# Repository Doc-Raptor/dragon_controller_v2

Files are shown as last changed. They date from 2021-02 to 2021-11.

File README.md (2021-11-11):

This is a controller-board for 3d printers based on the LPC1768 and has five tmc2209 onboard. It is made for the Marlin Firmware and RepRapFirmware. It has a Port to plug a Demos D1 Mini directly on it or a Raspberry Pi can be connected to with just jumpercables (no resistors needed).
IT IS NOT FULLY TESTED!!!
NO FURTHER DEVELOPMENT. RepRapFirmware discountinues support for the LPC1768

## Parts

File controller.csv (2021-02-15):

ID | Bezeichner | Gehäuse | Stückzahl | Bezeichnung | Anbieter und Referenz
1 | J1 | PinHeader_1x07_P2.54mm_Vertical | 1 | EXP3
2 | R9,R26,R25,R23,R20,R16,R15,R13,R10,R8 | R_1206_3216Metric | 10 | 0R11
3 | R37,R22,R21,R18,R12,R36 | R_1206_3216Metric | 6 | 4K7
4 | J24 | PinHeader_1x03_P2.54mm_Vertical | 1 | TH_E1
5 | C59,C16,C15,C19 | C_1206_3216Metric | 4 | 10uF
6 | Y1 | Crystal_SMD_5032-2Pin_5.0x3.2mm | 1 | 12Mhz
7 | U8,U7,U6,U5,U4 | QFN-28-1EP_5x5mm_P0.5mm_EP3.35x3.35mm_ThermalVias | 5 | TMC2209-LA
8 | U2 | LQFP-100_14x14mm_P0.5mm | 1 | LPC1768FBD100
9 | U1 | SOT-23-6 | 1 | MP2451
10 | SW1 | SW_Push_SPST_NO_Alps_SKRK | 1 | SW_Push
11 | R34,R33 | R_1206_3216Metric | 2 | 33K
12 | R32 | R_1206_3216Metric | 1 | 1K5
13 | R31,R30,R29,R28,R7,R3 | R_1206_3216Metric | 6 | 10K
14 | R27,R24,R19,R14,R6,R2 | R_1206_3216Metric | 6 | 1K
15 | R17,R11,R35 | R_1206_3216Metric | 3 | 100
16 | Q5 | SOT-23 | 1 | IRLML2244
17 | Q3,Q1,Q4 | TO-263-3_TabPin2 | 3 | SE30150
18 | Q2 | SOT-23 | 1 | PMV40UN2
19 | L2 | L_0805_2012Metric | 1 | 22uH
20 | J20 | PinHeader_1x04_P2.54mm_Vertical | 1 | e0-Stepper
21 | J44 | PinHeader_1x04_P2.54mm_Vertical | 1 | z-Stepper
22 | J43 | PinHeader_1x02_P2.54mm_Vertical | 1 | VCC
23 | J39 | PinHeader_1x04_P2.54mm_Vertical | 1 | y-Stepper
24 | J33 | PinHeader_1x04_P2.54mm_Vertical | 1 | x-Stepper
25 | J32 | microSD_HC_Hirose_DM3AT-SF-PEJM5 | 1 | Micro_SD_Card
26 | J31 | PinHeader_1x04_P2.54mm_Vertical | 1 | Serial
27 | J30 | PinHeader_2x05_P2.54mm_Vertical | 1 | EXP2
28 | J29 | PinHeader_2x05_P2.54mm_Vertical | 1 | EXP1
29 | J22 | PinHeader_1x02_P2.54mm_Vertical | 1 | USB_5V
30 | J21 | PinHeader_1x04_P2.54mm_Vertical | 1 | USB
31 | J19 | PinHeader_1x04_P2.54mm_Vertical | 1 | e1-Stepper
32 | J18 | PinHeader_1x01_P2.54mm_Vertical | 1 | DIAG_E1
33 | J17 | PinHeader_1x03_P2.54mm_Vertical | 1 | X-
34 | J16 | PinHeader_1x03_P2.54mm_Vertical | 1 | MAX_END
35 | J15 | PinHeader_1x03_P2.54mm_Vertical | 1 | Y-
36 | J13 | PinHeader_1x03_P2.54mm_Vertical | 1 | Z-
37 | J12 | PinHeader_1x02_P2.54mm_Vertical | 1 | DIAG_Z
38 | J11 | PinHeader_1x02_P2.54mm_Vertical | 1 | DIAG_Y
39 | J10 | PhoenixContact_GMSTBVA_2,5_2-G-7,62_1x02_P7.62mm_Vertical | 1 | Power_Heat
40 | J9 | PinHeader_1x01_P2.54mm_Vertical | 1 | DIAG_E0
41 | J8 | PinHeader_1x02_P2.54mm_Vertical | 1 | Fan_Cooler
42 | J7 | PinHeader_1x03_P2.54mm_Vertical | 1 | SV1
43 | J6 | PinHeader_1x03_P2.54mm_Vertical | 1 | TH_B
44 | J5,J23 | PhoenixContact_MCV_1,5_2-G-5.08_1x02_P5.08mm_Vertical | 2 | Hotend
45 | J4 | PinHeader_1x02_P2.54mm_Vertical | 1 | DIAG_X
46 | J3 | PhoenixContact_GMSTBVA_2,5_2-G-7,62_1x02_P7.62mm_Vertical | 1 | Power_IN
47 | J2 | PinHeader_1x03_P2.54mm_Vertical | 1 | TH_E0
48 | H4,H3,H2,H1 | MountingHole_3.2mm_M3 | 4 | MountingHole
49 | F1 | Fuseholder_Blade_ATO_Littelfuse_Pudenz_2_Pin | 1 | Fuse_Power
50 | D11,D8,D2,D3 | D_SOD-123 | 4 | 1N5819
51 | C58,C57,C17,C14 | C_0603_1608Metric | 4 | 12pF
52 | C56,C45,C39,C33,C27 | C_1206_3216Metric | 5 | 2.2uF
53 | C55,C54,C52,C51,C49,C48,C47,C46,C43,C42,C41,C40,C37,C36,C35,C34,C31,C30,C29,C25,C18,C1 | C_1206_3216Metric | 22 | 100nF
54 | C53,C26,C24,C22,C20 | CP_Elec_6.3x7.7 | 5 | 100uF
55 | C50,C44,C38,C32,C28 | C_0603_1608Metric | 5 | 22nF
56 | C23,C21,C13,C12,C11,C10,C9,C8,C7,C6 | C_0805_2012Metric | 10 | 0.1uF
57 | J46 | PinHeader_1x02_P2.54mm_Vertical | 1 | 3.3V
58 | J45 | PinHeader_1x02_P2.54mm_Vertical | 1 | 5V
59 | C2 | C_1206_3216Metric | 1 | 4.7uF
60 | C3,C4 | C_0805_2012Metric | 2 | 1uF
61 | C5 | C_0603_1608Metric | 1 | 33pF
62 | D1 | D_SMA | 1 | B140-13-F
63 | L1 | L_1812_4532Metric | 1 | 4.7uH
64 | R1 | R_1206_3216Metric | 1 | 124K
65 | R4 | R_1206_3216Metric | 1 | 23K7
66 | U3 | SOT-23-5 | 1 | RT9013-33GB
67 | R5 | R_1206_3216Metric | 1 | 100K
68 | TP1 | TestPoint_Pad_D1.0mm | 1 | RT1
69 | TP2 | TestPoint_Pad_D1.0mm | 1 | RT2
70 | TP3 | TestPoint_Pad_D1.0mm | 1 | RO
71 | TP4 | TestPoint_Pad_D1.0mm | 1 | TCK
72 | TP5 | TestPoint_Pad_D1.0mm | 1 | TRS
73 | TP6 | TestPoint_Pad_D1.0mm | 1 | TMS
74 | TP7 | TestPoint_Pad_D1.0mm | 1 | TDI
75 | TP8 | TestPoint_Pad_D1.0mm | 1 | TDO
76 | TP9 | TestPoint_Pad_D1.0mm | 1 | RTK

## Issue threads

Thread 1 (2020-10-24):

Und läuft es...

leseaw, 2020-10-24:
Moin Meister,
es sieht ja ganz guta us von der Idee her.
Nur funktioniert es auch?
Oder eher noch pre-apha??

Doc-Raptor, 2021-01-23:
Ich habe gestern geschaft, das der Mikrocontroller den Bootloader angenommen hat. Ich habe für eine Zeit das Projekt pausiert, damit ich nach einiger Zeit mit einem klaren Kopf drangehen zu können. Ich habe es aber auch dann nicht geschaft, das der Mikrocontroller funktionierte, also habe ich in mehreren Foren gefragt. Meistens kamen die nur mit irgendwelchen Tutorial, wie man mit Flash Magic das Ding flasht, die ich schon kannte, bis einer im eevblog Forum empfohlen hat, den Bootpin auf Low für den Flashvorgang auf Low zu halten anstatt wie überall steht den nur nach dem man Reset gedrückt hat kurzdarauf den Bootpin wieder loszulassen und dann den Flashvorgang zu starten. Ich bin auch dabei das Board paar Änderungen zu verpassen, was ein neues Board bedeutet. Der Teil mit den Stepper Drivern ist noch nicht getestet, ich hofe aber das ich das nächste Woche schaffe, wenn die Chips da sind.

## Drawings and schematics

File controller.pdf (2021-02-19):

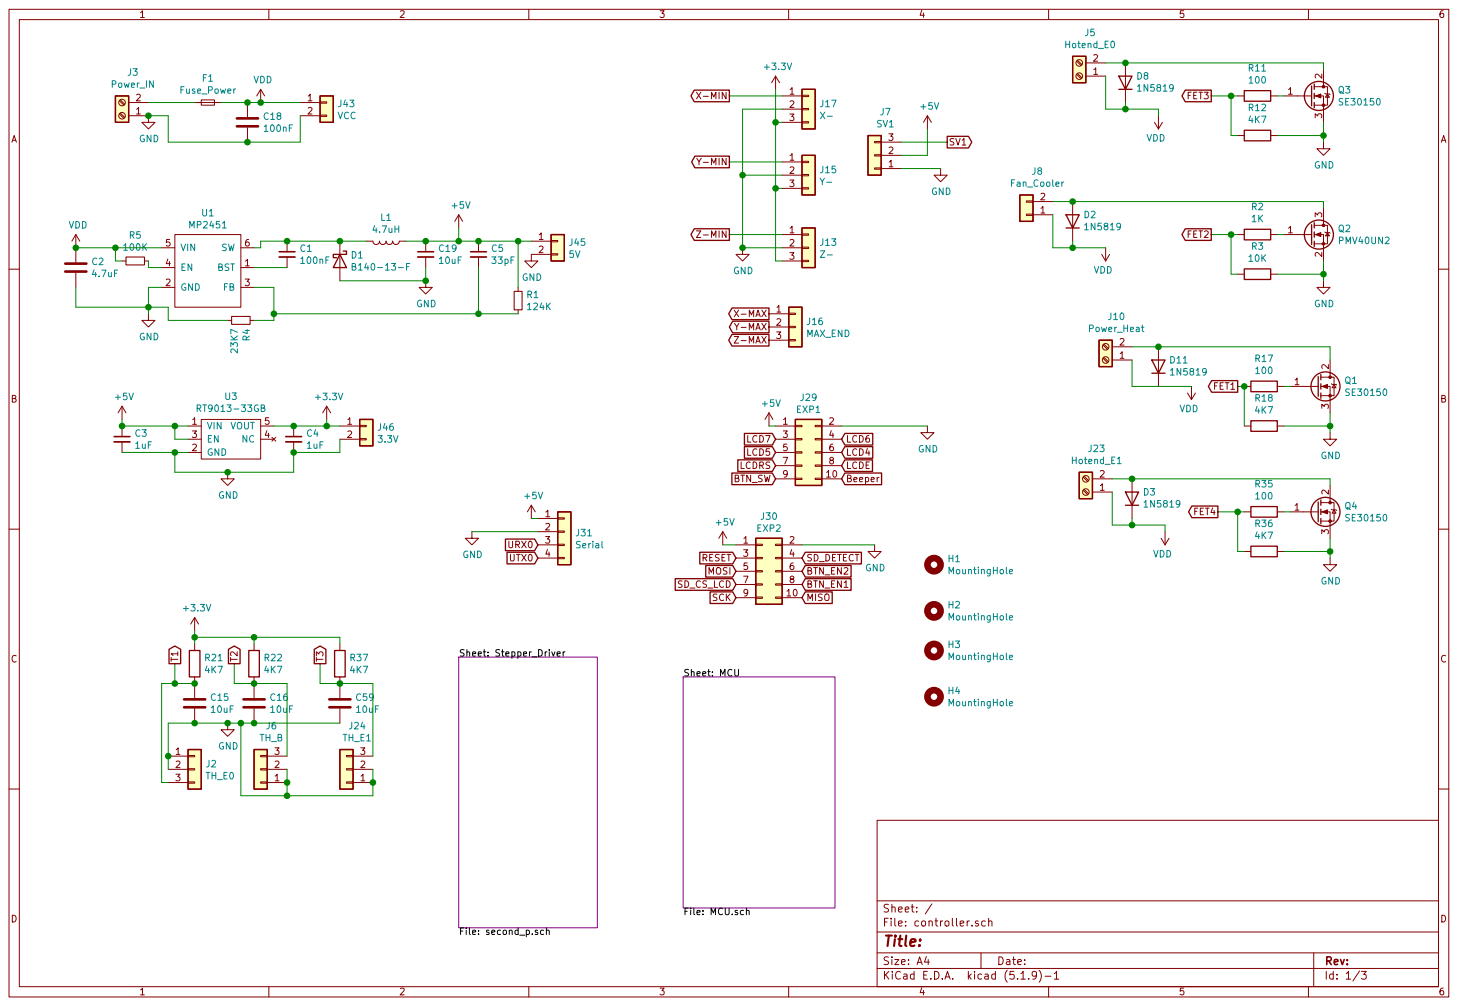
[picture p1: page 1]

File: MCU.sch Sheet: Stepper_Driver

Id: 1/3 Title: File: controller.sch Sheet: / Sheet: MCU

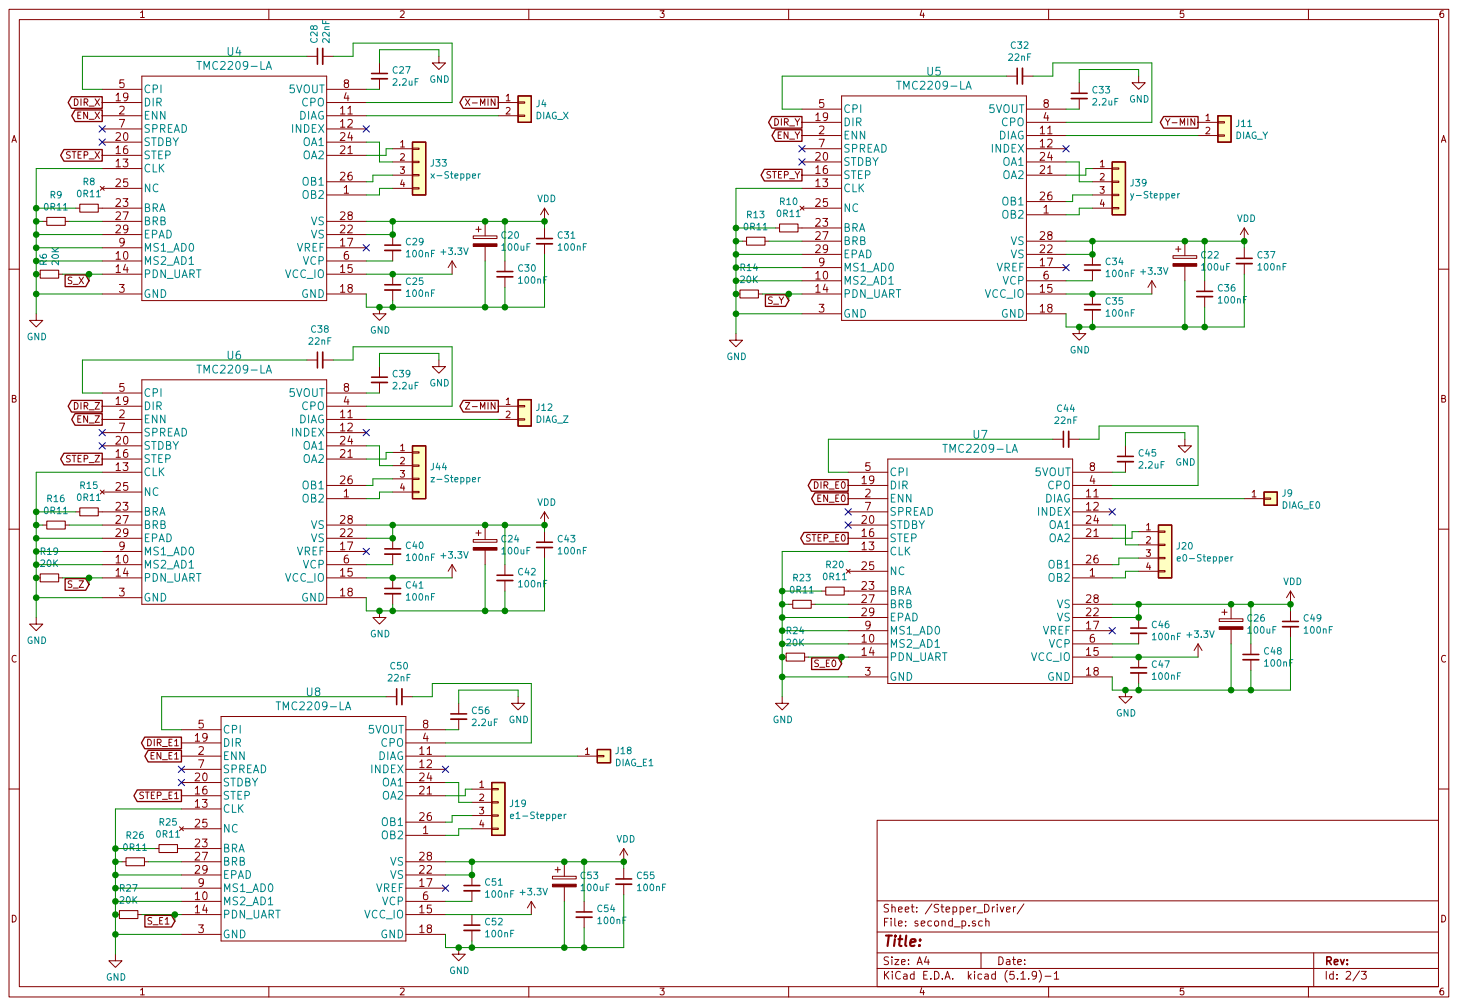
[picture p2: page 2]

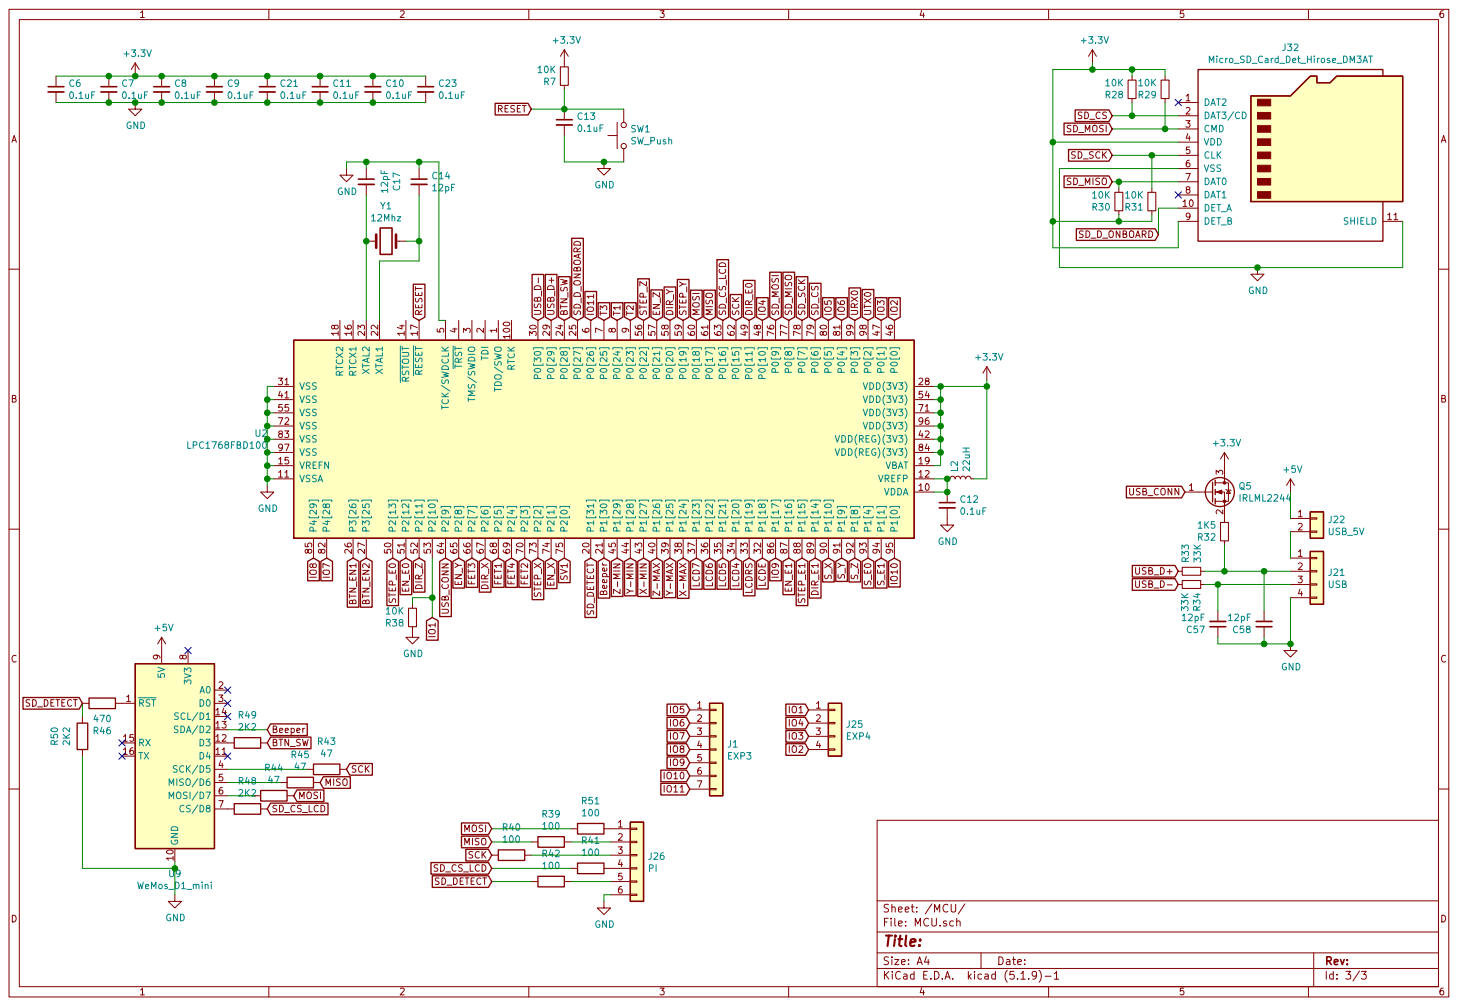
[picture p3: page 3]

1 VDDA 10 RTCK 100 VSSA 11 VREFP 12 RSTOUT 14 VREFN 15 RTCX1 16 RESET 17 RTCX2 18 VBAT 19 TDI 2 P1[31] 20 P1[30] 21 XTAL1 22 XTAL2 23 P0[28] 24 P0[27] 25 P3[26] 26 P3[25] 27

4 P1[26] 40 VSS 41 VDD(REG)(3V3) 42 P1[27] 43 P1[28] 44 P1[29] 45 P0[0] 46 P0[1] 47 P0[10] 48 P0[11] 49 TCK/SWDCLK

Id: 3/3 Title: File: MCU.sch Sheet: /MCU/

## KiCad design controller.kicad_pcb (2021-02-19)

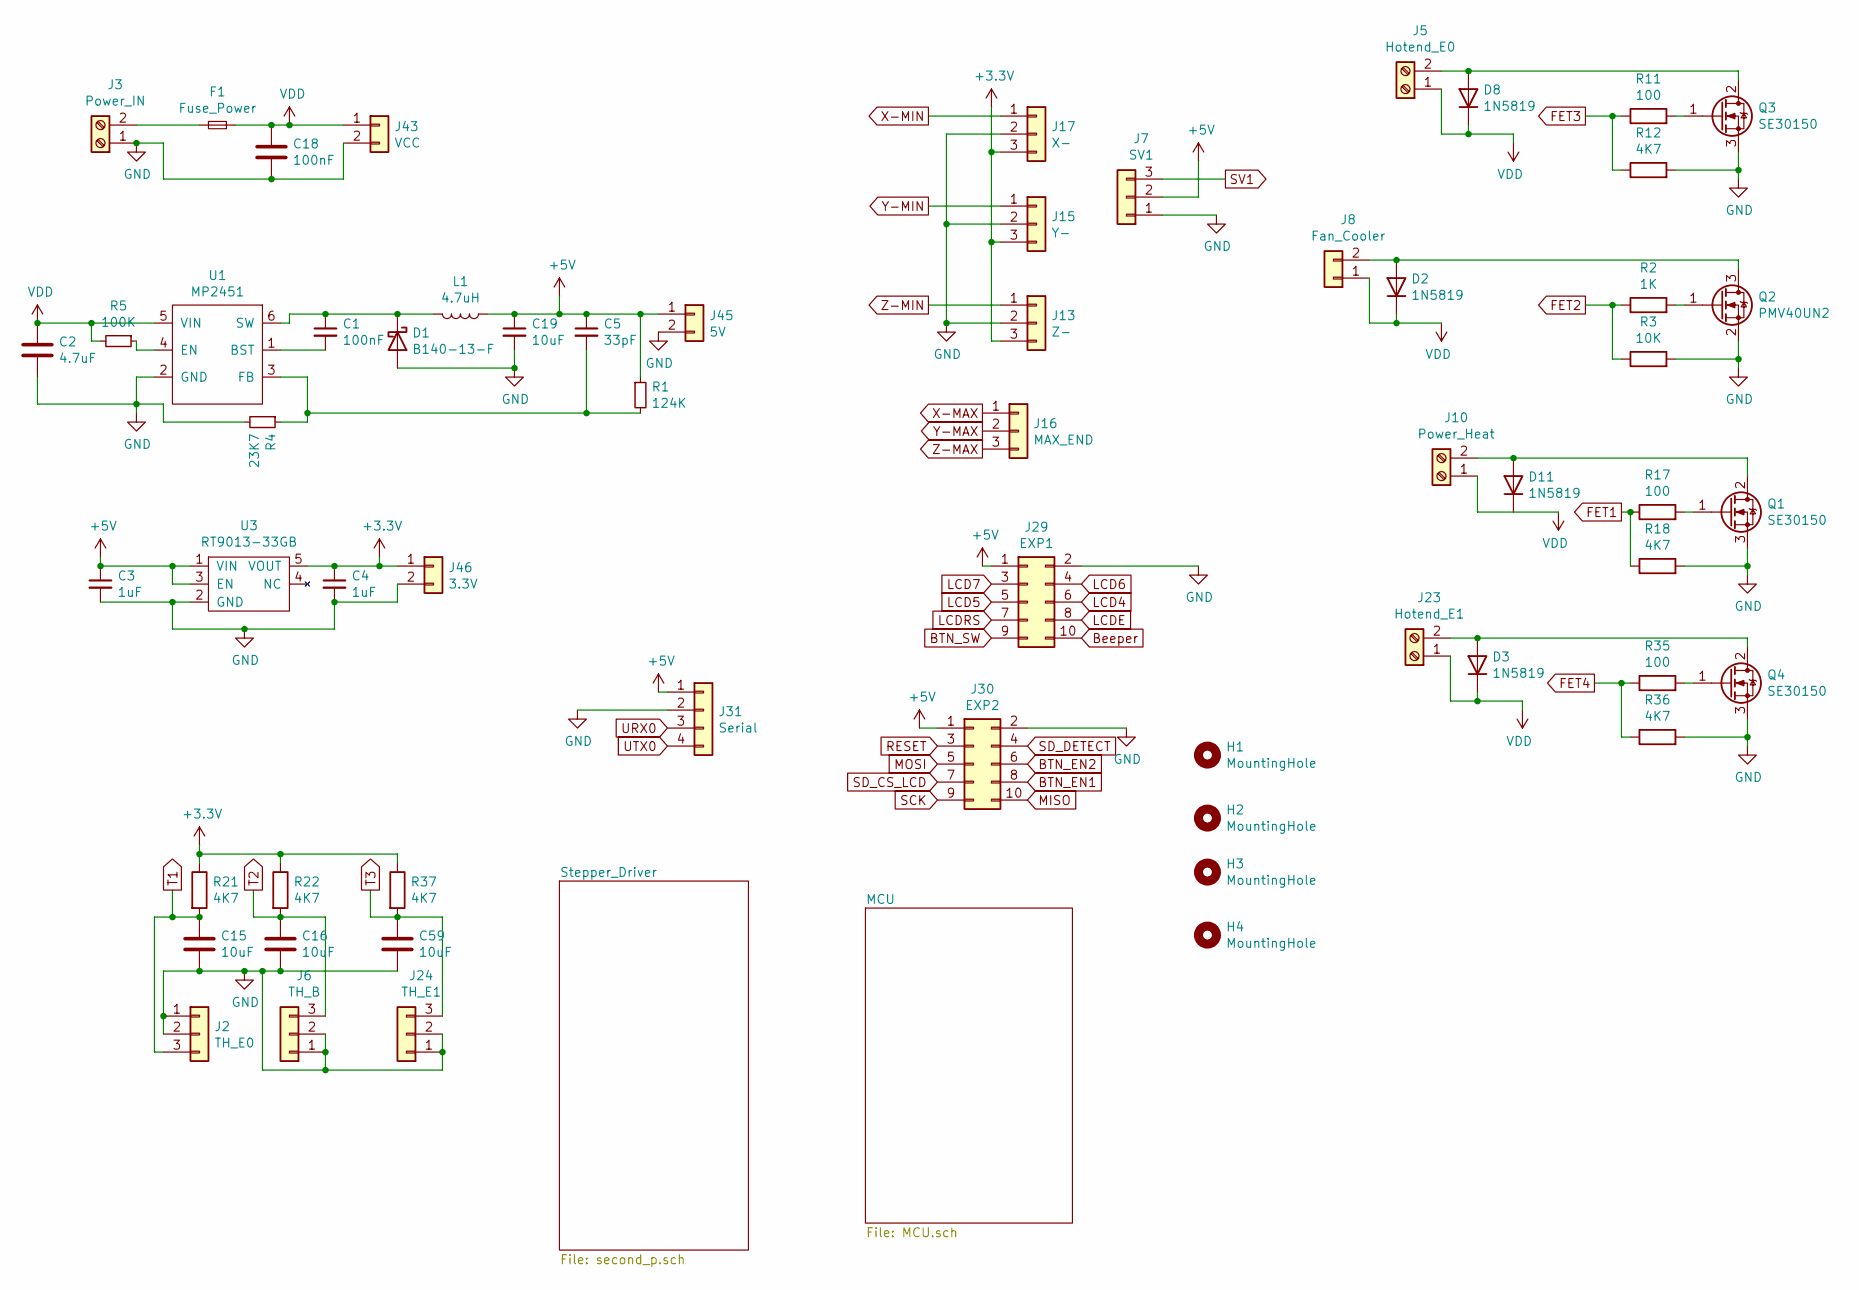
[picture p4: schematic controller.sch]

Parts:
C1, C18: 100nF; C_1206_3216Metric
C2: 4.7uF; C_1206_3216Metric
C3, C4: 1uF; C_0805_2012Metric
C5: 33pF; C_0603_1608Metric
C15, C16, C19, C59: 10uF; C_1206_3216Metric
D1: B140-13-F; D_SMA
D2, D3, D8, D11: 1N5819; D_SOD-123
F1: Fuse_Power; Fuseholder_Blade_Mini_Keystone_3568
H1, H2, H3, H4: MountingHole; MountingHole_3.2mm_M3
J2: TH_E0; PinHeader_1x03_P2.54mm_Vertical
J3: Power_IN; PhoenixContact_GMSTBVA_2,5_2-G-7,62_1x02_P7.62mm_Vertical
J5: Hotend_E0; PhoenixContact_MCV_1,5_2-G-5.08_1x02_P5.08mm_Vertical
J6: TH_B; PinHeader_1x03_P2.54mm_Vertical
J7: SV1; PinHeader_1x03_P2.54mm_Vertical
J8: Fan_Cooler; PinHeader_1x02_P2.54mm_Vertical
J10: Power_Heat; PhoenixContact_GMSTBVA_2,5_2-G-7,62_1x02_P7.62mm_Vertical
J13: Z-; PinHeader_1x03_P2.54mm_Vertical
J15: Y-; PinHeader_1x03_P2.54mm_Vertical
J16: MAX_END; PinHeader_1x03_P2.54mm_Vertical
J17: X-; PinHeader_1x03_P2.54mm_Vertical
J23: Hotend_E1; PhoenixContact_MCV_1,5_2-G-5.08_1x02_P5.08mm_Vertical
J24: TH_E1; PinHeader_1x03_P2.54mm_Vertical
J29: EXP1; Multicomp_MC9A12-1034_2x05_P2.54mm_Vertical
J30: EXP2; Multicomp_MC9A12-1034_2x05_P2.54mm_Vertical
J31: Serial; PinHeader_1x04_P2.54mm_Vertical
J43: VCC; PinHeader_1x02_P2.54mm_Vertical
J45: 5V; PinHeader_1x02_P2.54mm_Vertical
J46: 3.3V; PinHeader_1x02_P2.54mm_Vertical
L1: 4.7uH; L_1812_4532Metric
Q1, Q3, Q4: SE30150; TO-263-3_TabPin2
Q2: PMV40UN2; SOT-23
R1: 124K; R_1206_3216Metric
R2: 1K; R_1206_3216Metric
R3: 10K; R_1206_3216Metric
R4: 23K7; R_1206_3216Metric
R5: 100K; R_1206_3216Metric
R11, R17, R35: 100; R_1206_3216Metric
R12, R18, R21, R22, R36, R37: 4K7; R_1206_3216Metric
U1: MP2451; SOT-23-6
U3: RT9013-33GB; SOT-23-5

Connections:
+3V3: C4.1, J13.3, J15.3, J17.3, J46.1, R21.1, R22.1, R37.1, U3.5 (VOUT); also elsewhere on the board
+5V: C3.1, C5.1, C19.1, J7.2, J29.1, J30.1, J31.1, J45.1, L1.1, R1.1, U3.1 (VIN), U3.3 (EN); also elsewhere on the board
BTN_EN1: J30.8; also elsewhere on the board
BTN_EN2: J30.6; also elsewhere on the board
BTN_SW: J29.9; also elsewhere on the board
Beeper: J29.10; also elsewhere on the board
FET1: R17.1, R18.1; also elsewhere on the board
FET2: R2.1, R3.1; also elsewhere on the board
FET3: R11.1, R12.1; also elsewhere on the board
FET4: R35.1, R36.1; also elsewhere on the board
GND: C2.2, C3.2, C4.2, C15.2, C16.2, C18.2, C19.2, C59.2, D1.2 (A), J2.1, J2.2, J3.1, J6.1, J6.2, J7.1, J13.2, J15.2, J17.2, J24.1, J24.2, J29.2, J30.2, J31.2, J43.2, J45.2, J46.2, Q1.3 (S), Q2.2 (S), Q3.3 (S), Q4.3 (S), R3.2, R4.2, R12.2, R18.2, R36.2, U1.2 (GND), U3.2 (GND); also elsewhere on the board
LCD4: J29.6; also elsewhere on the board
LCD5: J29.5; also elsewhere on the board
LCD6: J29.4; also elsewhere on the board
LCD7: J29.3; also elsewhere on the board
LCDE: J29.8; also elsewhere on the board
LCDRS: J29.7; also elsewhere on the board
MISO: J30.10; also elsewhere on the board
MOSI: J30.5; also elsewhere on the board
unnamed: C1.1, D1.1 (K), L1.2, U1.6 (SW)
unnamed: C1.2, U1.1 (BST)
unnamed: C5.2, R1.2, R4.1, U1.3 (FB)
unnamed: D2.2 (A), J8.2, Q2.3 (D)
unnamed: D3.2 (A), J23.2, Q4.2 (D)
unnamed: D8.2 (A), J5.2, Q3.2 (D)
unnamed: D11.2 (A), J10.2, Q1.2 (D)
unnamed: F1.1, J3.2
unnamed: Q1.1 (G), R17.2
unnamed: Q2.1 (G), R2.2
unnamed: Q3.1 (G), R11.2
unnamed: Q4.1 (G), R35.2
unnamed: R5.1, U1.4 (EN)
RESET: J30.3; also elsewhere on the board
SCK: J30.9; also elsewhere on the board
SD_CS_LCD: J30.7; also elsewhere on the board
SD_DETECT: J30.4; also elsewhere on the board
SV1: J7.3; also elsewhere on the board
T1: C15.1, J2.3, R21.2; also elsewhere on the board
T2: C16.1, J6.3, R22.2; also elsewhere on the board
T3: C59.1, J24.3, R37.2; also elsewhere on the board
URX0: J31.3; also elsewhere on the board
UTX0: J31.4; also elsewhere on the board
VDD: C2.1, C18.1, D2.1 (K), D3.1 (K), D8.1 (K), D11.1 (K), F1.2, J5.1, J8.1, J10.1, J23.1, J43.1, R5.2, U1.5 (VIN); also elsewhere on the board
X-MAX: J16.1; also elsewhere on the board
X-MIN: J17.1; also elsewhere on the board
Y-MAX: J16.2; also elsewhere on the board
Y-MIN: J15.1; also elsewhere on the board
Z-MAX: J16.3; also elsewhere on the board
Z-MIN: J13.1; also elsewhere on the board

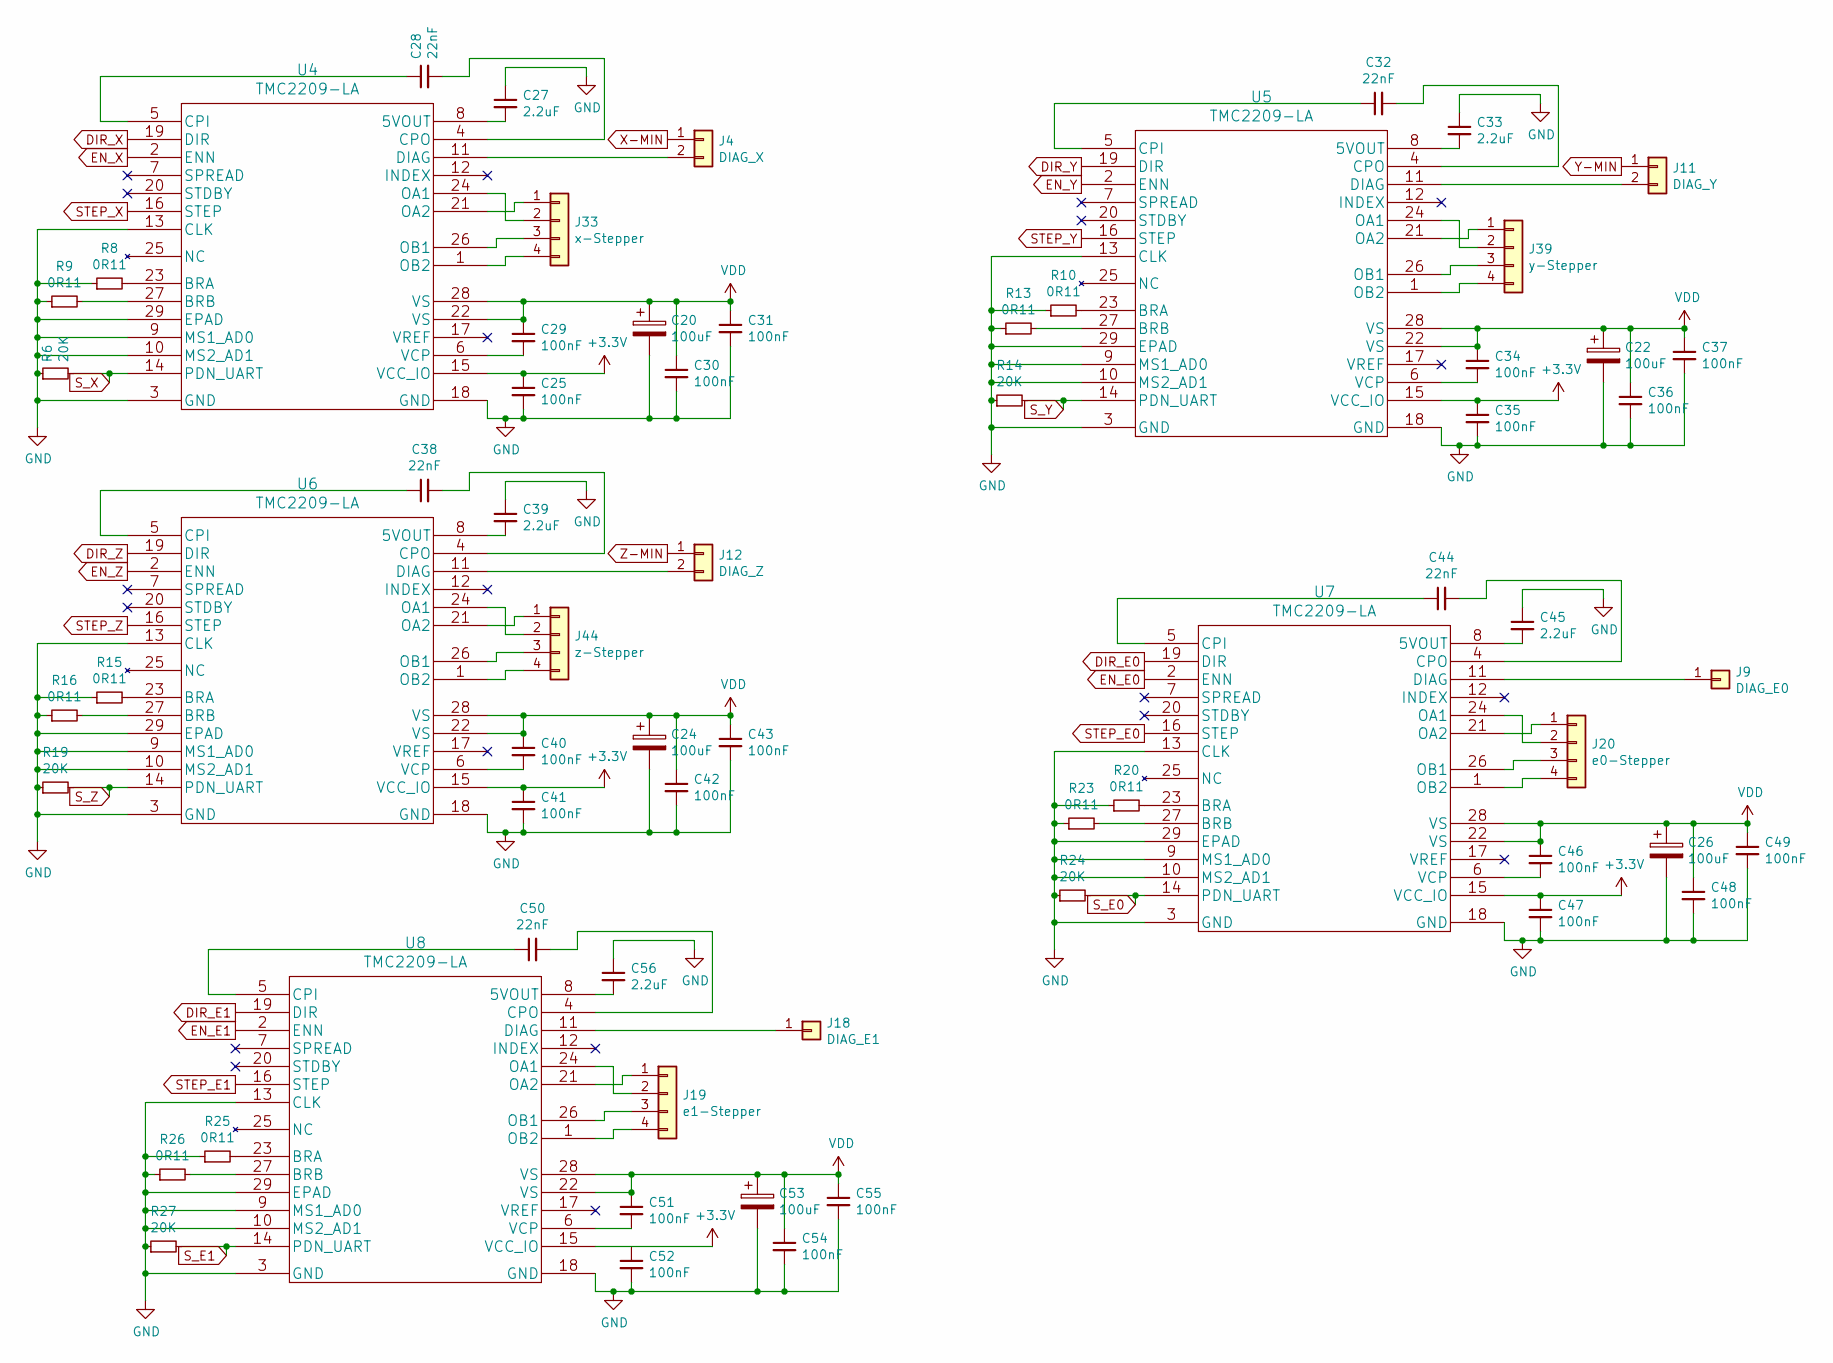
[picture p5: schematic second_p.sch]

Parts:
C20, C22, C24, C26, C53: 100uF; CP_Elec_6.3x7.7
C25, C29, C30, C31, C34, C35, C36, C37, C40, C41, C42, C43, C46, C47, C48, C49, C51, C52, C54, C55: 100nF; C_1206_3216Metric
C27, C33, C39, C45, C56: 2.2uF; C_1206_3216Metric
C28, C32, C38, C44, C50: 22nF; C_0603_1608Metric
J4: DIAG_X; PinHeader_1x02_P2.54mm_Vertical
J9: DIAG_E0; PinHeader_1x01_P2.54mm_Vertical
J11: DIAG_Y; PinHeader_1x02_P2.54mm_Vertical
J12: DIAG_Z; PinHeader_1x02_P2.54mm_Vertical
J18: DIAG_E1; PinHeader_1x01_P2.54mm_Vertical
J19: e1-Stepper; PinHeader_1x04_P2.54mm_Vertical
J20: e0-Stepper; PinHeader_1x04_P2.54mm_Vertical
J33: x-Stepper; PinHeader_1x04_P2.54mm_Vertical
J39: y-Stepper; PinHeader_1x04_P2.54mm_Vertical
J44: z-Stepper; PinHeader_1x04_P2.54mm_Vertical
R6, R14, R19, R24, R27: 20K; R_1206_3216Metric
R8, R9, R10, R13, R15, R16, R20, R23, R25, R26: 0R11; R_1206_3216Metric
U4, U5, U6, U7, U8: TMC2209-LA; QFN-28-1EP_5x5mm_P0.5mm_EP3.35x3.35mm_ThermalVias

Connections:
+3V3: C25.1, C35.1, C41.1, C47.1, C52.1, U4.15 (VCC_IO), U5.15 (VCC_IO), U6.15 (VCC_IO), U7.15 (VCC_IO), U8.15 (VCC_IO); also elsewhere on the board
DIR_E0: U7.19 (DIR); also elsewhere on the board
DIR_E1: U8.19 (DIR); also elsewhere on the board
DIR_X: U4.19 (DIR); also elsewhere on the board
DIR_Y: U5.19 (DIR); also elsewhere on the board
DIR_Z: U6.19 (DIR); also elsewhere on the board
EN_E0: U7.2 (ENN); also elsewhere on the board
EN_E1: U8.2 (ENN); also elsewhere on the board
EN_X: U4.2 (ENN); also elsewhere on the board
EN_Y: U5.2 (ENN); also elsewhere on the board
EN_Z: U6.2 (ENN); also elsewhere on the board
GND: C20.2, C22.2, C24.2, C25.2, C26.2, C27.1, C30.2, C31.2, C33.1, C35.2, C36.2, C37.2, C39.1, C41.2, C42.2, C43.2, C45.1, C47.2, C48.2, C49.2, C52.2, C53.2, C54.2, C55.2, C56.1, R6.1, R8.1, R9.1, R10.1, R13.1, R14.1, R15.1, R16.1, R19.1, R20.1, R23.1, R24.1, R25.1, R26.1, R27.1, U4.3 (GND), U4.9 (MS1_AD0), U4.10 (MS2_AD1), U4.13 (CLK), U4.18 (GND), U4.29 (EPAD), U5.3 (GND), U5.9 (MS1_AD0), U5.10 (MS2_AD1), U5.13 (CLK), U5.18 (GND), U5.29 (EPAD), U6.3 (GND), U6.9 (MS1_AD0), U6.10 (MS2_AD1), U6.13 (CLK), U6.18 (GND), U6.29 (EPAD), U7.3 (GND), U7.9 (MS1_AD0), U7.10 (MS2_AD1), U7.13 (CLK), U7.18 (GND), U7.29 (EPAD), U8.3 (GND), U8.9 (MS1_AD0), U8.10 (MS2_AD1), U8.13 (CLK), U8.18 (GND), U8.29 (EPAD); also elsewhere on the board
unnamed: C27.2, U4.8 (5VOUT)
unnamed: C28.1, U4.5 (CPI)
unnamed: C28.2, U4.4 (CPO)
unnamed: C29.2, U4.6 (VCP)
unnamed: C32.1, U5.5 (CPI)
unnamed: C32.2, U5.4 (CPO)
unnamed: C33.2, U5.8 (5VOUT)
unnamed: C34.2, U5.6 (VCP)
unnamed: C38.1, U6.5 (CPI)
unnamed: C38.2, U6.4 (CPO)
unnamed: C39.2, U6.8 (5VOUT)
unnamed: C40.2, U6.6 (VCP)
unnamed: C44.1, U7.5 (CPI)
unnamed: C44.2, U7.4 (CPO)
unnamed: C45.2, U7.8 (5VOUT)
unnamed: C46.2, U7.6 (VCP)
unnamed: C50.1, U8.5 (CPI)
unnamed: C50.2, U8.4 (CPO)
unnamed: C51.2, U8.6 (VCP)
unnamed: C56.2, U8.8 (5VOUT)
unnamed: J4.2, U4.11 (DIAG)
unnamed: J9.1, U7.11 (DIAG)
unnamed: J11.2, U5.11 (DIAG)
unnamed: J12.2, U6.11 (DIAG)
unnamed: J18.1, U8.11 (DIAG)
unnamed: J19.1, U8.21 (OA2)
unnamed: J19.2, U8.24 (OA1)
unnamed: J19.3, U8.26 (OB1)
unnamed: J19.4, U8.1 (OB2)
unnamed: J20.1, U7.21 (OA2)
unnamed: J20.2, U7.24 (OA1)
unnamed: J20.3, U7.26 (OB1)
unnamed: J20.4, U7.1 (OB2)
unnamed: J33.1, U4.21 (OA2)
unnamed: J33.2, U4.24 (OA1)
unnamed: J33.3, U4.26 (OB1)
unnamed: J33.4, U4.1 (OB2)
unnamed: J39.1, U5.21 (OA2)
unnamed: J39.2, U5.24 (OA1)
unnamed: J39.3, U5.26 (OB1)
unnamed: J39.4, U5.1 (OB2)
unnamed: J44.1, U6.21 (OA2)
unnamed: J44.2, U6.24 (OA1)
unnamed: J44.3, U6.26 (OB1)
unnamed: J44.4, U6.1 (OB2)
unnamed: R8.2, U4.23 (BRA)
unnamed: R9.2, U4.27 (BRB)
unnamed: R10.2, U5.23 (BRA)
unnamed: R13.2, U5.27 (BRB)
unnamed: R15.2, U6.23 (BRA)
unnamed: R16.2, U6.27 (BRB)
unnamed: R20.2, U7.23 (BRA)
unnamed: R23.2, U7.27 (BRB)
unnamed: R25.2, U8.23 (BRA)
unnamed: R26.2, U8.27 (BRB)
STEP_E0: U7.16 (STEP); also elsewhere on the board
STEP_E1: U8.16 (STEP); also elsewhere on the board
STEP_X: U4.16 (STEP); also elsewhere on the board
STEP_Y: U5.16 (STEP); also elsewhere on the board
STEP_Z: U6.16 (STEP); also elsewhere on the board
S_E0: R24.2, U7.14 (PDN_UART); also elsewhere on the board
S_E1: R27.2, U8.14 (PDN_UART); also elsewhere on the board
S_X: R6.2, U4.14 (PDN_UART); also elsewhere on the board
S_Y: R14.2, U5.14 (PDN_UART); also elsewhere on the board
S_Z: R19.2, U6.14 (PDN_UART); also elsewhere on the board
VDD: C20.1, C22.1, C24.1, C26.1, C29.1, C30.1, C31.1, C34.1, C36.1, C37.1, C40.1, C42.1, C43.1, C46.1, C48.1, C49.1, C51.1, C53.1, C54.1, C55.1, U4.22 (VS), U4.28 (VS), U5.22 (VS), U5.28 (VS), U6.22 (VS), U6.28 (VS), U7.22 (VS), U7.28 (VS), U8.22 (VS), U8.28 (VS); also elsewhere on the board
X-MIN: J4.1; also elsewhere on the board
Y-MIN: J11.1; also elsewhere on the board
Z-MIN: J12.1; also elsewhere on the board

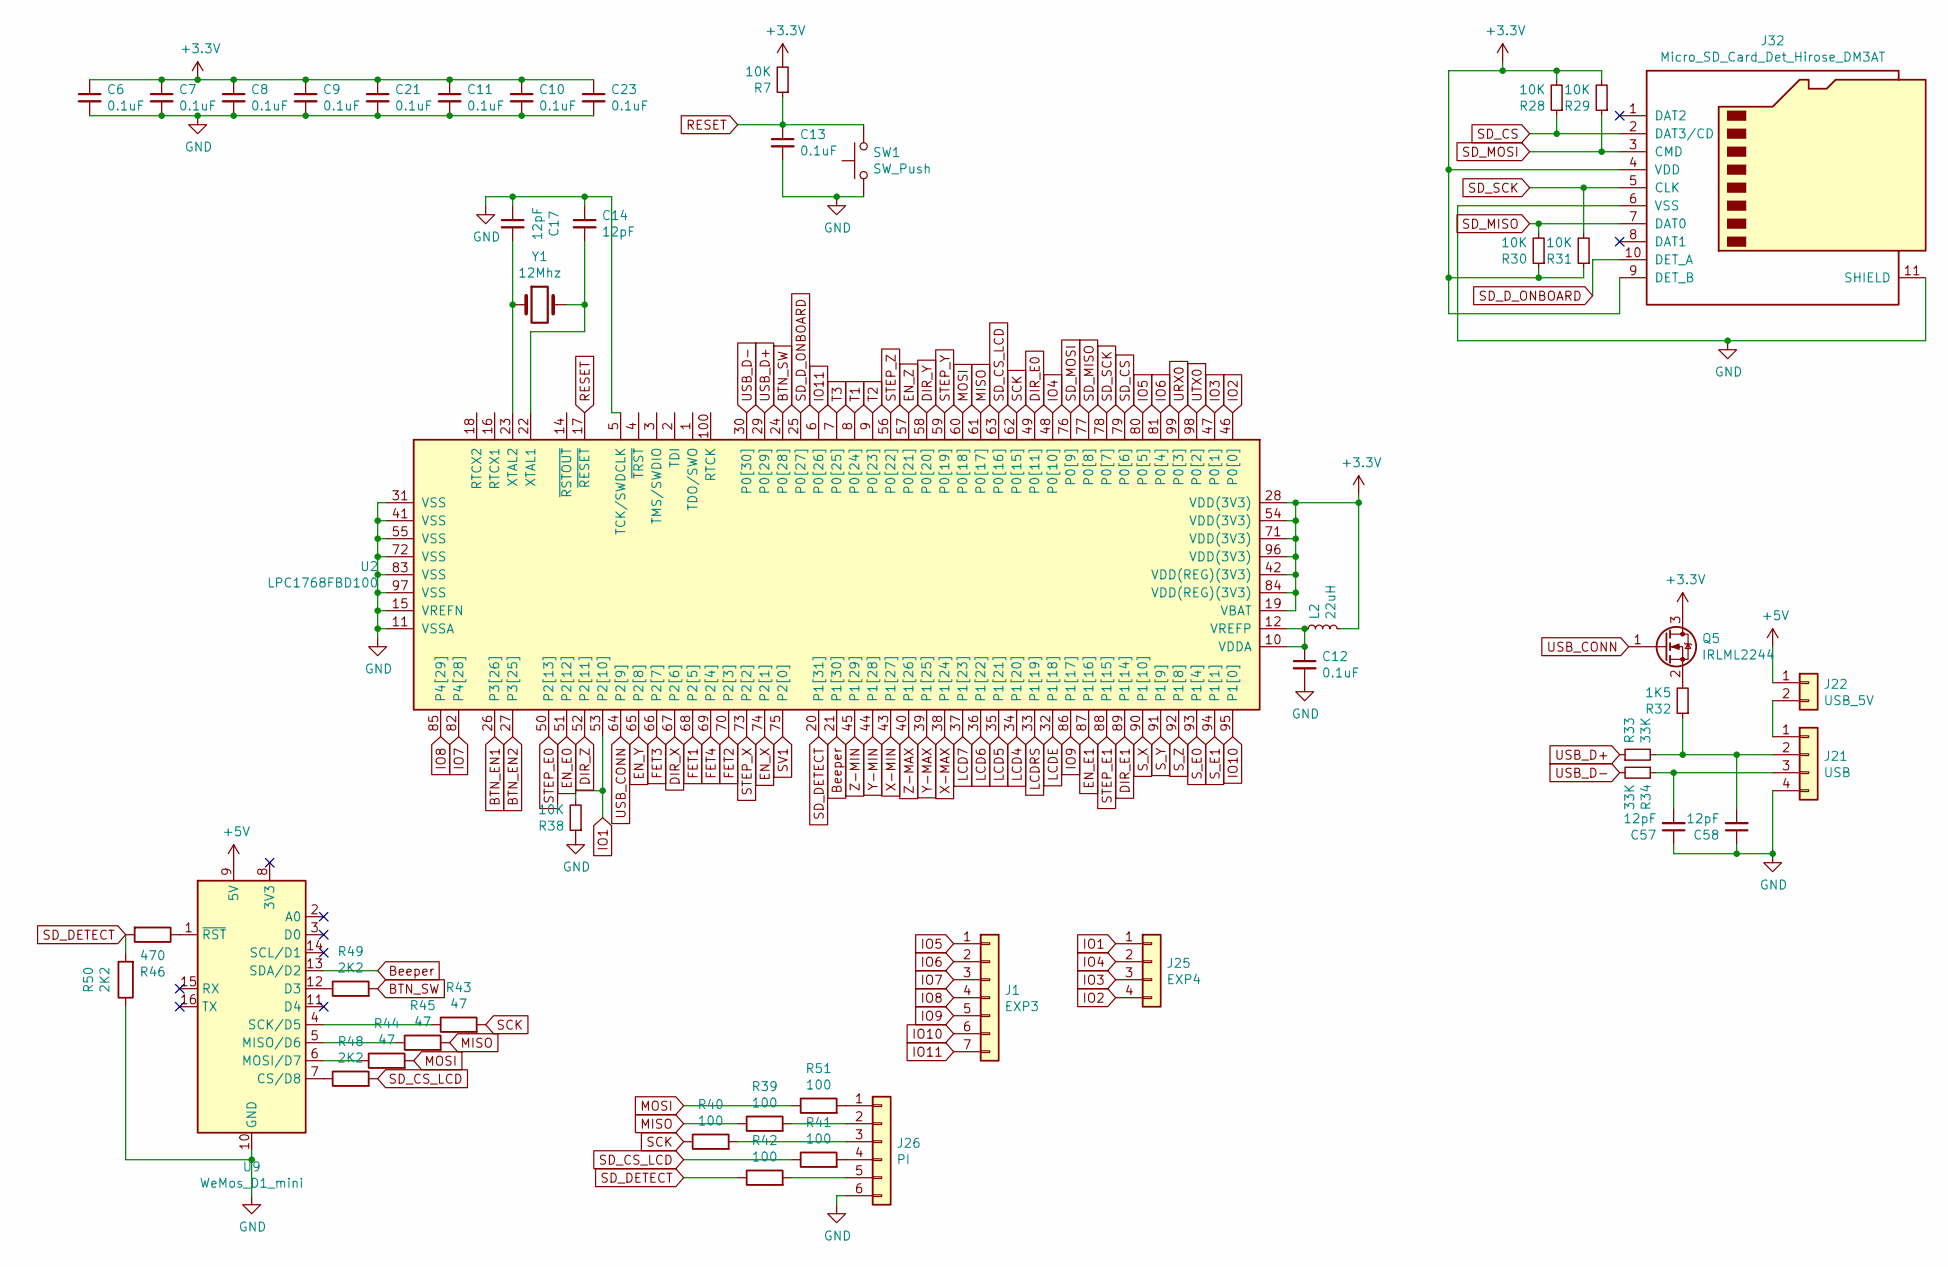
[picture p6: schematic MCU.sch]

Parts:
C6, C7, C8, C9, C10, C11, C12, C13, C21, C23: 0.1uF; C_0805_2012Metric
C14, C17, C57, C58: 12pF; C_0603_1608Metric
J1: EXP3; PinHeader_1x07_P2.54mm_Vertical
J21: USB; PinHeader_1x04_P2.54mm_Vertical
J22: USB_5V; PinHeader_1x02_P2.54mm_Vertical
J25: EXP4; PinHeader_1x04_P2.54mm_Vertical
J26: PI; PinHeader_1x06_P2.54mm_Vertical
J32: Micro_SD_Card_Det_Hirose_DM3AT; microSD_HC_Hirose_DM3AT-SF-PEJM5
L2: 22uH; L_0805_2012Metric
Q5: IRLML2244; SOT-23
R7, R28, R29, R30, R31, R38: 10K; R_1206_3216Metric
R32: 1K5; R_1206_3216Metric
R33, R34: 33K; R_1206_3216Metric
R39, R40, R41, R42, R51: 100; R_1206_3216Metric
R43, R44, R45: 47; R_1206_3216Metric
R46: 470; R_1206_3216Metric
R48, R49, R50: 2K2; R_1206_3216Metric
SW1: SW_Push; SW_Push_SPST_NO_Alps_SKRK
U2: LPC1768FBD100; LQFP-100_14x14mm_P0.5mm
U9: WeMos_D1_mini; WEMOS_D1_mini_light
Y1: 12Mhz; Crystal_SMD_5032-2Pin_5.0x3.2mm

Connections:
+3V3: C6.1, C7.1, C8.1, C9.1, C10.1, C11.1, C21.1, C23.1, J32.4 (VDD), J32.9 (DET_B), L2.2, Q5.3 (D), R7.2, R28.2, R29.2, R30.1, R31.1, U2.19 (VBAT), U2.28 (VDD(3V3)), U2.42 (VDD(REG)(3V3)), U2.54 (VDD(3V3)), U2.71 (VDD(3V3)), U2.84 (VDD(REG)(3V3)), U2.96 (VDD(3V3)); also elsewhere on the board
+5V: J22.1, U9.9 (5V); also elsewhere on the board
BTN_EN1: U2.26 (P3[26]); also elsewhere on the board
BTN_EN2: U2.27 (P3[25]); also elsewhere on the board
BTN_SW: R49.2, U2.24 (P0[28]); also elsewhere on the board
Beeper: U2.21 (P1[30]), U9.13 (SDA/D2); also elsewhere on the board
DIR_E0: U2.49 (P0[11]); also elsewhere on the board
DIR_E1: U2.89 (P1[14]); also elsewhere on the board
DIR_X: U2.67 (P2[6]); also elsewhere on the board
DIR_Y: U2.58 (P0[20]); also elsewhere on the board
DIR_Z: U2.52 (P2[11]); also elsewhere on the board
EN_E0: U2.51 (P2[12]); also elsewhere on the board
EN_E1: U2.87 (P1[16]); also elsewhere on the board
EN_X: U2.74 (P2[1]); also elsewhere on the board
EN_Y: U2.65 (P2[8]); also elsewhere on the board
EN_Z: U2.57 (P0[21]); also elsewhere on the board
FET1: U2.68 (P2[5]); also elsewhere on the board
FET2: U2.70 (P2[3]); also elsewhere on the board
FET3: U2.66 (P2[7]); also elsewhere on the board
FET4: U2.69 (P2[4]); also elsewhere on the board
GND: C6.2, C7.2, C8.2, C9.2, C10.2, C11.2, C12.2, C13.2, C14.1, C17.1, C21.2, C23.2, C57.1, C58.1, J21.4, J26.6, J32.6 (VSS), J32.11 (SHIELD), R38.1, R50.1, SW1.1, U2.5 (TCK/SWDCLK), U2.11 (VSSA), U2.15 (VREFN), U2.31 (VSS), U2.41 (VSS), U2.55 (VSS), U2.72 (VSS), U2.83 (VSS), U2.97 (VSS), U9.10 (GND); also elsewhere on the board
IO1: J25.1, R38.2, U2.53 (P2[10])
IO2: J25.4, U2.46 (P0[0])
IO3: J25.3, U2.47 (P0[1])
IO4: J25.2, U2.48 (P0[10])
IO5: J1.1, U2.80 (P0[5])
IO6: J1.2, U2.81 (P0[4])
IO7: J1.3, U2.82 (P4[28])
IO8: J1.4, U2.85 (P4[29])
IO9: J1.5, U2.86 (P1[17])
IO10: J1.6, U2.95 (P1[0])
IO11: J1.7, U2.6 (P0[26])
LCD4: U2.34 (P1[20]); also elsewhere on the board
LCD5: U2.35 (P1[21]); also elsewhere on the board
LCD6: U2.36 (P1[22]); also elsewhere on the board
LCD7: U2.37 (P1[23]); also elsewhere on the board
LCDE: U2.32 (P1[18]); also elsewhere on the board
LCDRS: U2.33 (P1[19]); also elsewhere on the board
MISO: R39.1, R45.2, U2.61 (P0[17]); also elsewhere on the board
MOSI: R44.2, R51.1, U2.60 (P0[18]); also elsewhere on the board
unnamed: C12.1, L2.1, U2.10 (VDDA), U2.12 (VREFP)
unnamed: C14.2, U2.22 (XTAL1), Y1.2
unnamed: C17.2, U2.23 (XTAL2), Y1.1
unnamed: C57.2, J21.3, R34.1
unnamed: C58.2, J21.2, R32.1, R33.2
unnamed: J21.1, J22.2
unnamed: J26.1, R51.2
unnamed: J26.2, R39.2
unnamed: J26.3, R40.2
unnamed: J26.4, R41.2
unnamed: J26.5, R42.2
unnamed: Q5.2 (S), R32.2
unnamed: R43.1, U9.4 (SCK/D5)
unnamed: R44.1, U9.6 (MOSI/D7)
unnamed: R45.1, U9.5 (MISO/D6)
unnamed: R46.1, U9.1 (~RST)
unnamed: R48.1, U9.7 (CS/D8)
unnamed: R49.1, U9.12 (D3)
RESET: C13.1, R7.1, SW1.2, U2.17 (~RESET~); also elsewhere on the board
SCK: R40.1, R43.2, U2.62 (P0[15]); also elsewhere on the board
SD_CS: J32.2 (DAT3/CD), R28.1, U2.79 (P0[6])
SD_CS_LCD: R41.1, R48.2, U2.63 (P0[16]); also elsewhere on the board
SD_DETECT: R42.1, R46.2, R50.2, U2.20 (P1[31]); also elsewhere on the board
SD_D_ONBOARD: J32.10 (DET_A), U2.25 (P0[27])
SD_MISO: J32.7 (DAT0), R30.2, U2.77 (P0[8])
SD_MOSI: J32.3 (CMD), R29.1, U2.76 (P0[9])
SD_SCK: J32.5 (CLK), R31.2, U2.78 (P0[7])
STEP_E0: U2.50 (P2[13]); also elsewhere on the board
STEP_E1: U2.88 (P1[15]); also elsewhere on the board
STEP_X: U2.73 (P2[2]); also elsewhere on the board
STEP_Y: U2.59 (P0[19]); also elsewhere on the board
STEP_Z: U2.56 (P0[22]); also elsewhere on the board
SV1: U2.75 (P2[0]); also elsewhere on the board
S_E0: U2.93 (P1[4]); also elsewhere on the board
S_E1: U2.94 (P1[1]); also elsewhere on the board
S_X: U2.90 (P1[10]); also elsewhere on the board
S_Y: U2.91 (P1[9]); also elsewhere on the board
S_Z: U2.92 (P1[8]); also elsewhere on the board
T1: U2.8 (P0[24]); also elsewhere on the board
T2: U2.9 (P0[23]); also elsewhere on the board
T3: U2.7 (P0[25]); also elsewhere on the board
URX0: U2.99 (P0[3]); also elsewhere on the board
USB_CONN: Q5.1 (G), U2.64 (P2[9])
USB_D+: R33.1, U2.29 (P0[29])
USB_D-: R34.2, U2.30 (P0[30])
UTX0: U2.98 (P0[2]); also elsewhere on the board
X-MAX: U2.38 (P1[24]); also elsewhere on the board
X-MIN: U2.43 (P1[27]); also elsewhere on the board
Y-MAX: U2.39 (P1[25]); also elsewhere on the board
Y-MIN: U2.44 (P1[28]); also elsewhere on the board
Z-MAX: U2.40 (P1[26]); also elsewhere on the board
Z-MIN: U2.45 (P1[29]); also elsewhere on the board

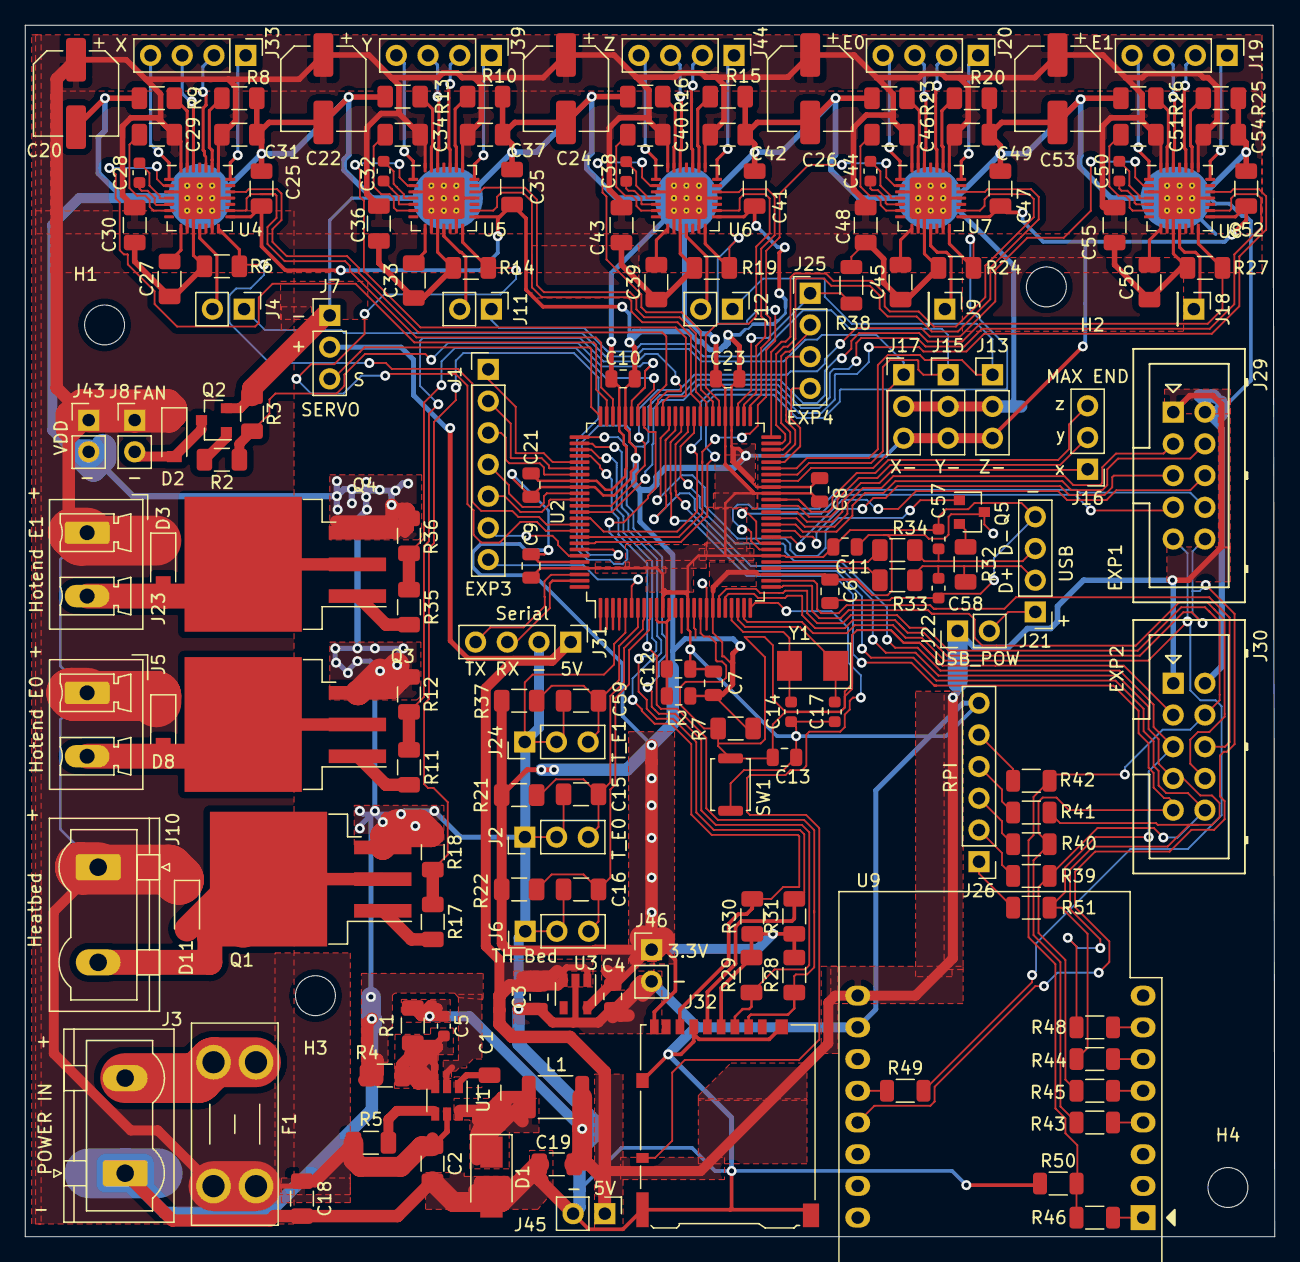
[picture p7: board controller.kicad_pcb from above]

Board: 2 copper layers, 100.1 x 97.0 mm, 172 parts (0 on the bottom side), 161 nets.

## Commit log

2020-08-30 Ready for test
    [MCU.sch, controller.kicad_pcb, controller.sch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]
2020-08-30 new files for manufacturing
    [controller-B_Cu.gbr, controller-B_Mask.gbr, controller-B_SilkS.gbr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]
2021-02-15 New PCB layout and some mods
    [BOM.xlsx, MCU.sch, bom_for_lcsc.csv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]
2021-02-16 Fix some mistakes
    [controller.kicad_pcb]
2021-02-19 Fix some stuff
    [controller-B_Cu.gbr, controller-B_Mask.gbr, controller-B_SilkS.gbr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]
